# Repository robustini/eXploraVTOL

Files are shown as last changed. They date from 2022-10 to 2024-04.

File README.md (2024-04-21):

# eXplora Tailsitter VTOL

**Every single printable part of the project can be viewed in 3D on [OnShape](https://cad.onshape.com/documents/4c689e5b54cac6902d5813ec/w/fb80a5d05358b4e7959139db/e/8ae4df59a9bf6fdd0ec86a21)**

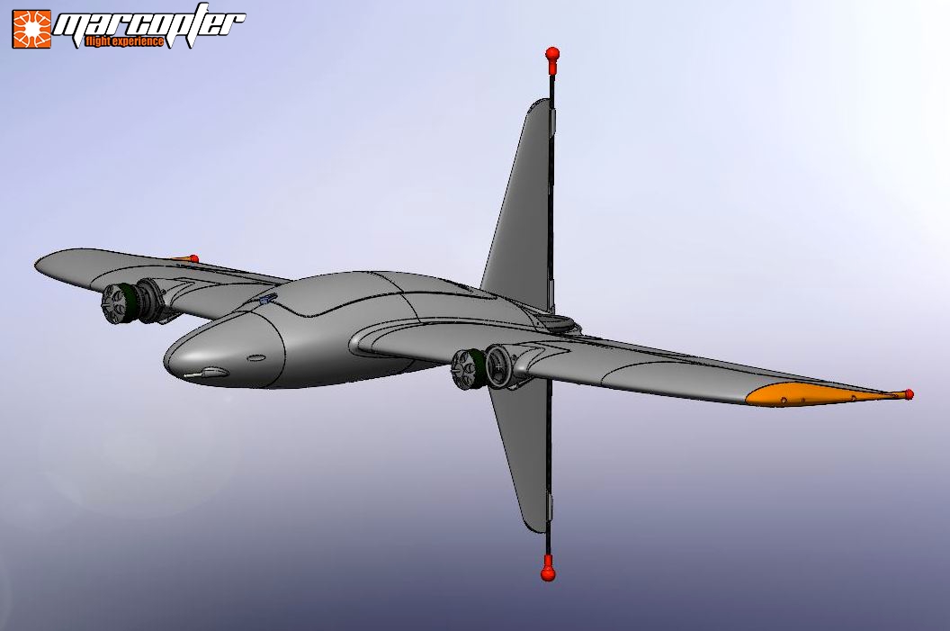
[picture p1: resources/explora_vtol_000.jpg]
eXplora Tailsitter VTOL


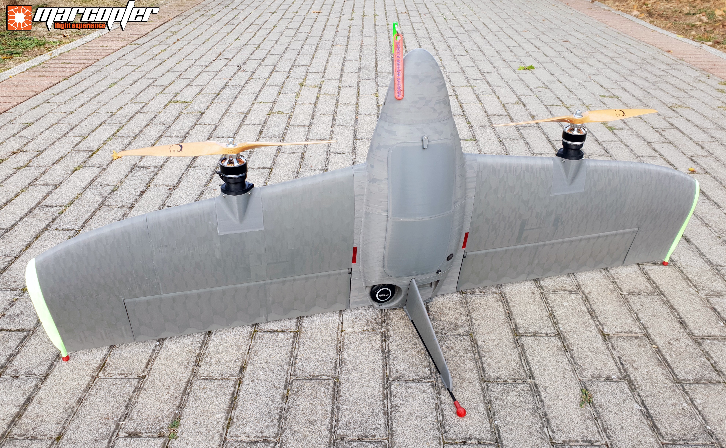
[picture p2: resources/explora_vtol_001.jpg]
eXplora Tailsitter VTOL


## Work in progress! ##

Given the massive requests we decided to make the repository public but it is still currently lacking documentation and specifications.

This will still give you the opportunity to view the entire project and print out all the individual components in order to finalize it.

We will complete the repository with everything we need as soon as possible.

To print the right wing you will need to mirror all the parts of the left wing in slicing, it is a very simple operation.

---

**eXplora Tailsitter VTOL** it was born from a concept by [Marco Robustini](https://www.linkedin.com/in/marco-robustini-a48a49a8/) four years ago.

Is a fully 3D printed vertical take-off UAS, a multi-role drone suitable for FPV, photogrammetry and other purposes, printed in PLA, ABS and TPU filament.

It comes in three formats: STL, 3MF and STEP, that way anyone can collaborate to improve it.

The slicing of this taislitter is complex, which is why all 3MF-format designs run with the powerful open source slicing software [SuperSlicer](https://github.com/supermerill/SuperSlicer) are provided.

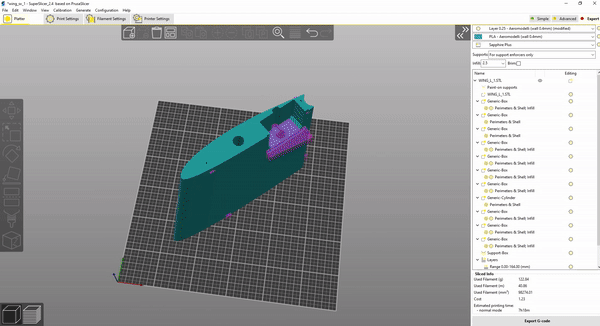
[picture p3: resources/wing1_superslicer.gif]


If you decide to use other slicing software such as [Cura](https://3dgbire.com/pages/ultimaker-cura) you should consider adding reinforcements at crucial points, taking a cue from the 3MF projects we provide as an example, compatible only with SuperSlicer and PrusaSlicer.
In this case you will not have to use this 3MFs but import the STLs into your slicing software.

We used the [Gyroid](https://3dsolved.com/3d-printing-with-gyroid-infills-all-you-need-to-know/) infill for most of the profiles, it comes from Nature, butterflies have an identical structure inside their wings, and Nature is never wrong.
It guarantees lightness and incredible strength.

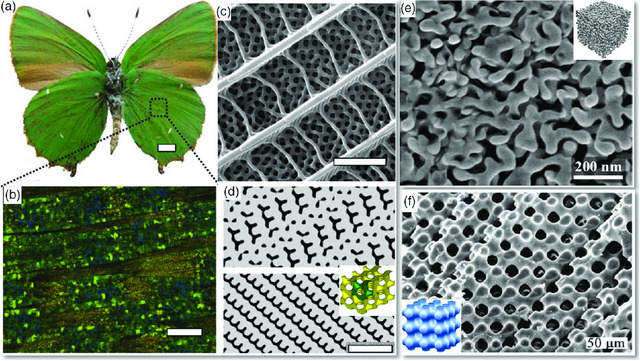
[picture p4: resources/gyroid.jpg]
Gyroid


## How it works and what it takes to finish it ##

eXplora Tailsitter VTOL it requires flight control and other electronic components to operate.

It has been tested with [Ardupilot](https://ardupilot.org) and [PX4](https://px4.io).

This is the provisional [BOM](https://github.com/robustini/eXploraVTOL/tree/main/resources/BOM.md) to complete the UAS, continuously being updated, absent for now of screws and nuts.

## Videos ##

- [The first version of eXplora](https://youtu.be/43UC-_kWp0w)
- [The second version of eXplora](https://youtu.be/K6R6v6_kQL0)
- [Flight tests of the V0.9.0](https://youtu.be/hy-UXrUSplU)
- [Full automatic mission](https://youtu.be/ne_7n9bvjYg)
- [Acro capability test](https://youtu.be/VbT0gd1w8IY)
- [Ardupilot: weathervaning feature](https://youtu.be/qcV7hz61uzA)
- [Ardupilot: QRTL](https://youtu.be/3Y-EviXewf0)

## User support ##

- [Discord channel](https://discord.gg/TCjNnfAEsB)
- [Ardupilot Discuss](https://discuss.ardupilot.org/t/explora-tailsitter-vtol-3d-printable-dual-motor-tailsitter/92341)

## How to get involved ##

- The eXplora Tailsitter VTOL project is open source and we encourage participation, if you can help in any way you are welcome!

- We have an active group of Beta Testers to help us improve our eXplora Tailsitter VTOL.

- Desired enhancements and issue can be posted to the [issues list](https://github.com/robustini/eXploraVTOL/issues).

- You can also open a [discussion](https://github.com/robustini/eXploraVTOL/discussions) to look for information or anything else.

## Simulation ##

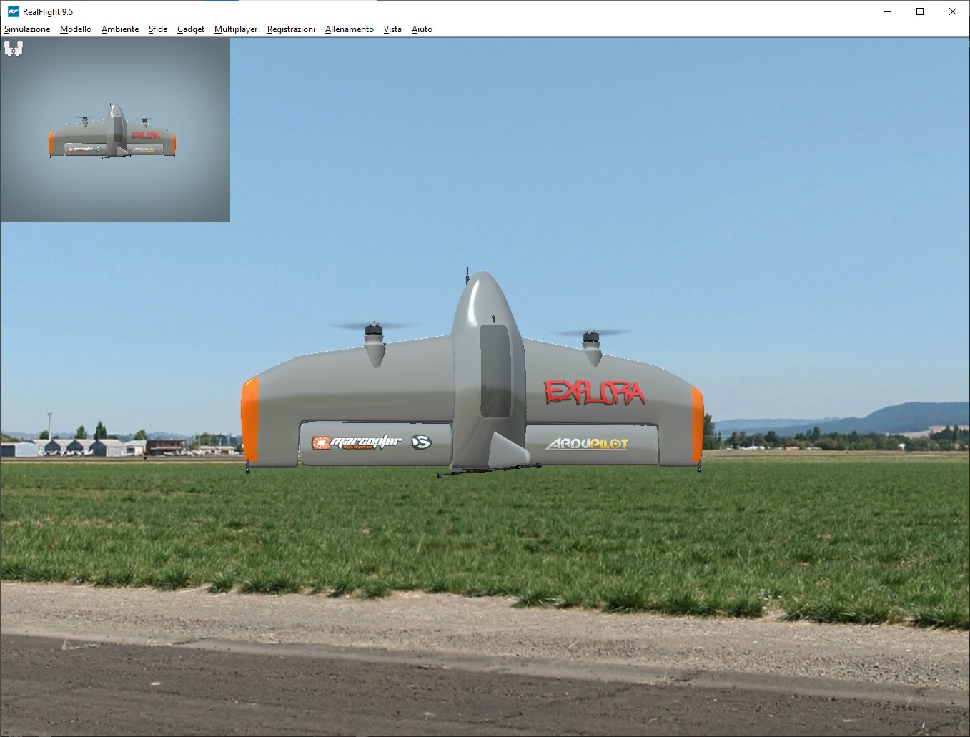
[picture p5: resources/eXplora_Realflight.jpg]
eXplora Tailsitter VTOL


If you would like to try our VTOL the [model](https://github.com/robustini/eXploraVTOL/tree/main/simulation/eXplora_Tailsiter_VTOL.RFX) for Realflight is available.

## The team ##

- [Davide Silimbani](https://www.linkedin.com/in/davide-silimbani/): 3d design
- [Roberto Casoni](https://www.linkedin.com/in/roberto-casoni-463a5914a/): test pilot
- [Lorenzo Franco](https://www.linkedin.com/in/lorenzing/): GCS support
- [Edoardo Nunzi](https://www.linkedin.com/in/edoardo-nunzi-8176a31a2/): FPV test pilot
- Antonios Antzoulatos: 3d print test
- [Brandon MacDougall](https://www.linkedin.com/in/brandon-macdougall-b273907/): Realflight model
- [Marco Robustini](https://www.linkedin.com/in/robustini/): concept design, SuperSlicer project, in-flight tuning and tests

## License ##

The eXplora Tailsitter VTOL project is licensed under the [GNU General Public License, version 3](https://github.com/robustini/eXploraVTOL/blob/main/LICENSE).

## Credits ##

We would like to publicly thank the development team of Ardupilot, and to all the beta testers who helped us.

## Donate ##

If you would like to support this project you can make a [donation](https://paypal.me/marcopter).

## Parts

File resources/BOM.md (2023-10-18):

# eXplora Tailsitter VTOL

## Bill of Materials ##

**Carbon tube:**

- 1 X Carbon tube: outer diameter 16mm, inner diameter 14mm, length 240mm
- 1 X Carbon tube: outer diameter 14mm, inner diameter 12mm, length 1000mm
- 2 X Carbon tube: outer diameter 10mm, inner diameter 8mm, length 469mm
- 2 X Carbon tube: outer diameter 5mm, inner diameter 3mm, length 43mm
- 1 X Carbon tube: outer diameter 5mm, inner diameter 3mm, length 600mm
- 2 X Carbon tube: outer diameter 4mm, inner diameter 2mm, length 56mm

**Propulsion:**

- 2 x GARTT ML 4112 480KV motor, or T-Motor Navigator MN4012 480kV, or equivalent (500W minimum)
- 2 x 14x8 beech wood propellers (length and pitch depend on the motor)
- 2 x 50A 6S ESC BlHeli32 with telemetry (alternatively 40A but not less)

**Servos:**

- 2 x SAVOX SC-1252MG Digital Servo (standard size) or equivalent/better

**Autopilot:**

- 1 x "Ardupilot" compatible flight control (Cube Orange, Pixhawk1 or equivalent), with its dedicated Power Module
- 1 x M8N GPS with compass, Here3 GPS GNSS, or better (alternatively double gps differently oriented)
- 1 x Airspeed Sensor MEAS Spec series (e.g. MS4525DO, MS5525), the analogs did not give good results
- 1 x BEC adequately sized on input/output voltage and maximum servo current, example input 25.2V (6S), output 6V, current 5A
- 1 x SiK Radio Telemetry or other type

**Optional:**

- 2 x JX8 connector, male and female
- 1 x TFmini Plus LIDAR

Various things, such as screws, nuts, power cables, servos extensions and others are not on the list at the moment, and still depend on the build type.

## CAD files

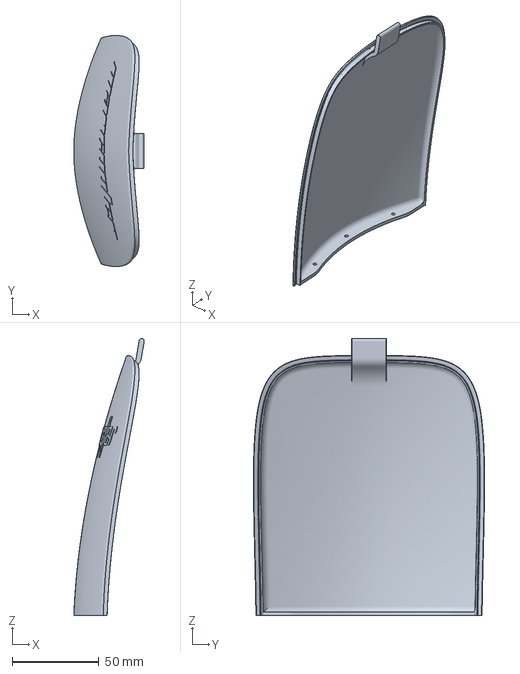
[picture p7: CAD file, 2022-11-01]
3MF/eXplora_VTOL_V1.00_Canopy_1.3mf
40.6 x 133.0 x 159.4 mm

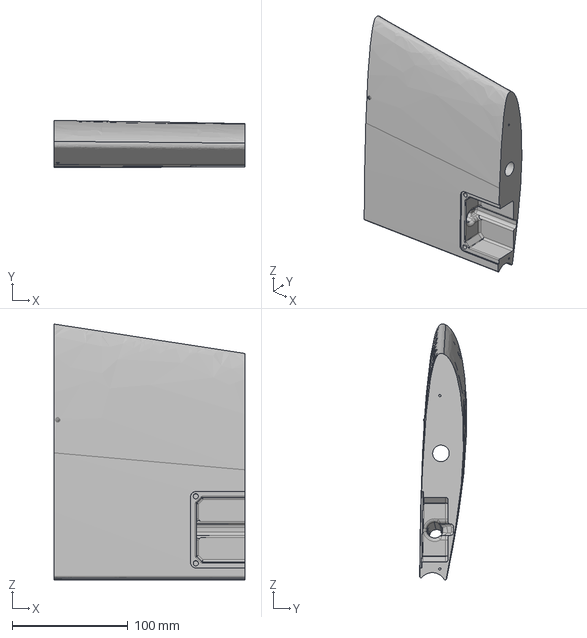
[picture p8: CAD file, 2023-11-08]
STEP/eXplora_VTOL_V1.00_Wing_L1.step
165.0 x 40.5 x 221.5 mm

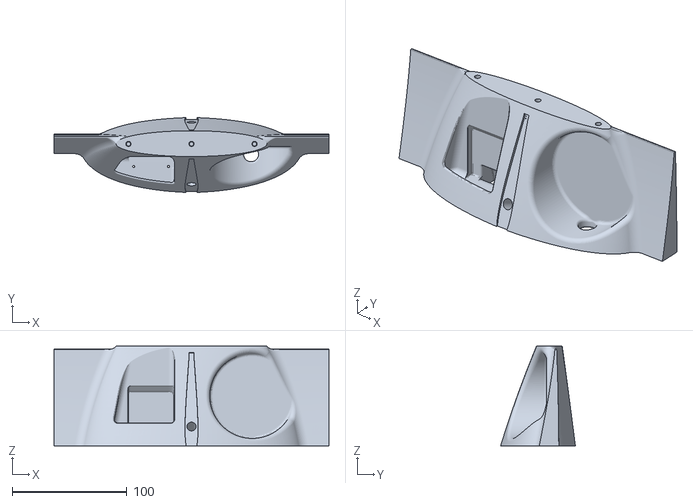
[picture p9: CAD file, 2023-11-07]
STL/eXplora_VTOL_V1.00_Fuselage_4_insert.stl
240.0 x 65.3 x 87.0

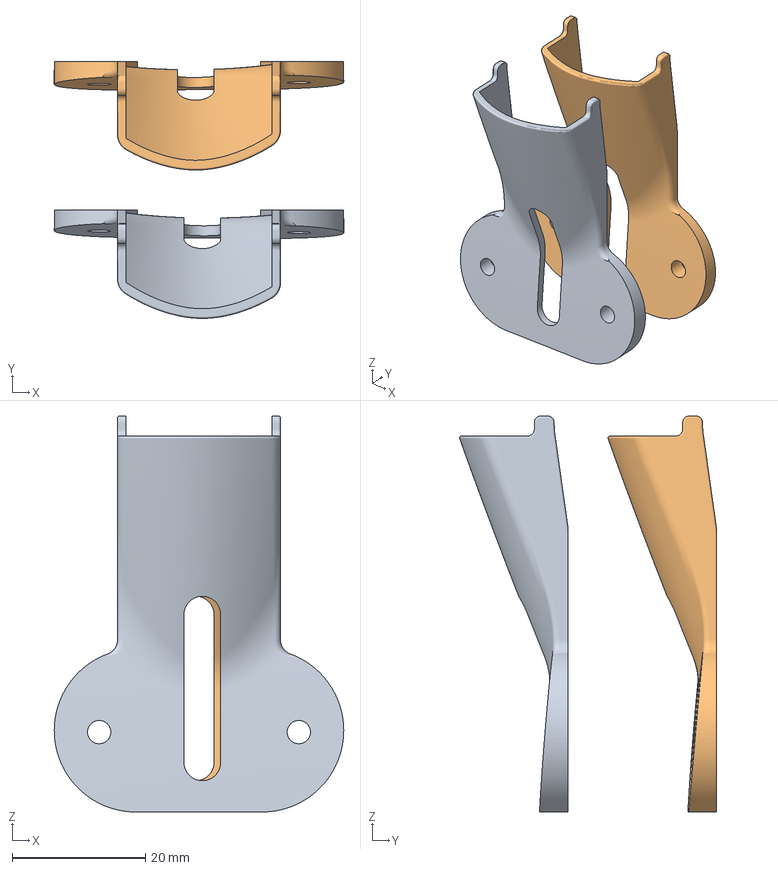
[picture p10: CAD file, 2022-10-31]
3MF/eXplora_VTOL_V1.00_ESC_cover_LR.3mf
43.5 x 38.6 x 59.5 mm
eXplora_VTOL_V1.00_ESC_cover_R.STL
eXplora_VTOL_V1.00_ESC_cover_L.STL

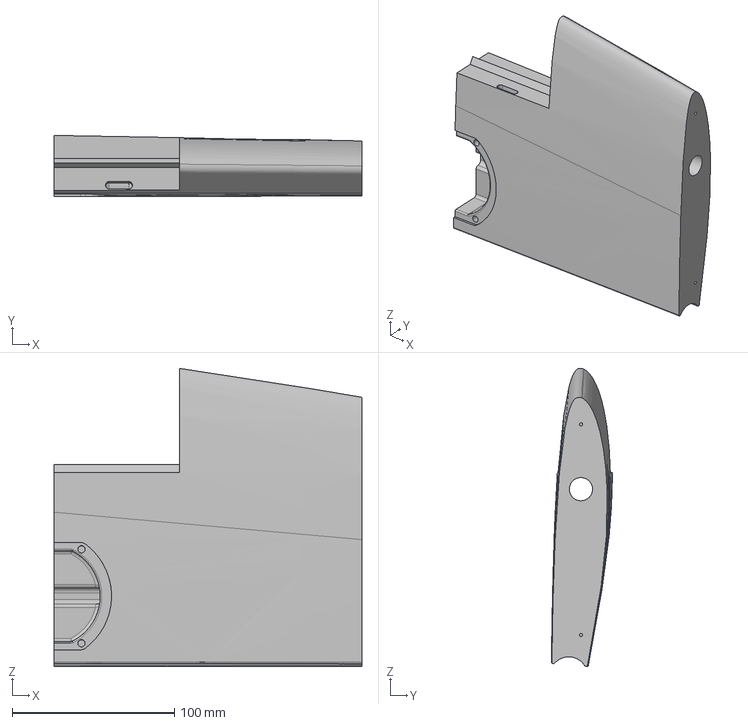
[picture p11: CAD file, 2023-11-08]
STEP/eXplora_VTOL_V1.00_Wing_L2.step
190.0 x 37.7 x 184.0 mm

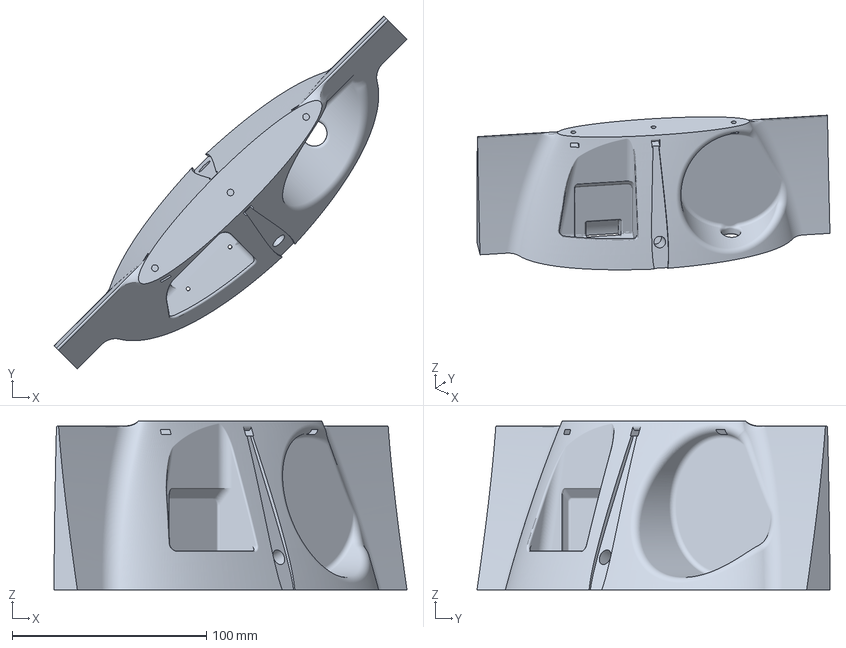
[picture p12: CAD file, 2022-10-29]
3MF/eXplora_VTOL_V1.00_Fuselage_4.3mf
181.7 x 181.7 x 87.0 mm

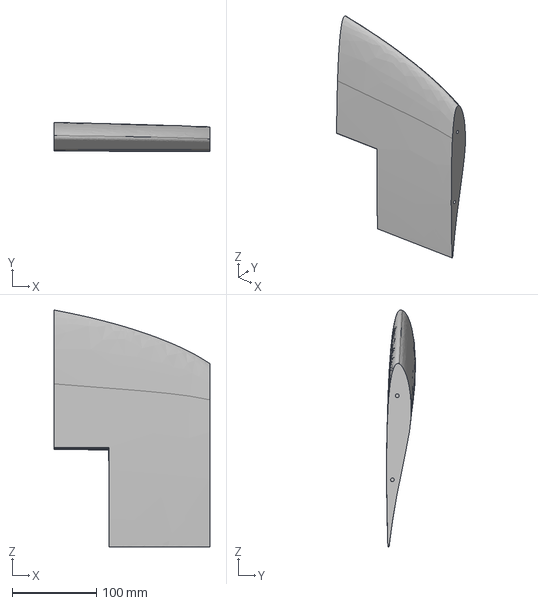
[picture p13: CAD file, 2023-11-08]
STEP/eXplora_VTOL_V1.00_Wing_L4.step
185.0 x 34.5 x 281.7 mm

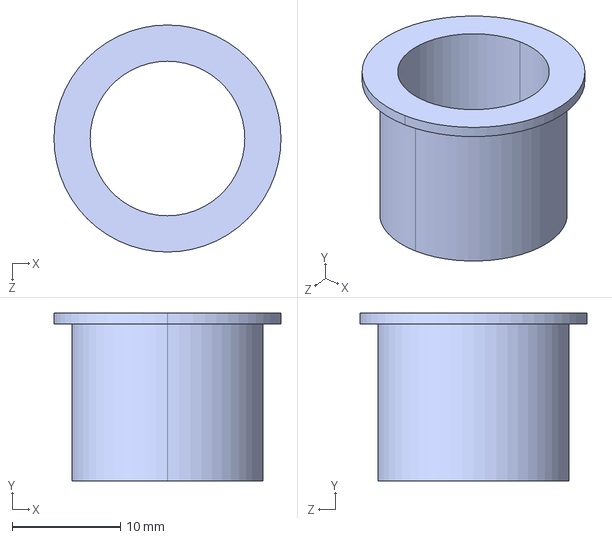
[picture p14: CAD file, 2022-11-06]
STEP/eXplora_VTOL_V1.00_14mm_Bayonet_Adapter_LR.step
21.0 x 15.5 x 21.0 mm

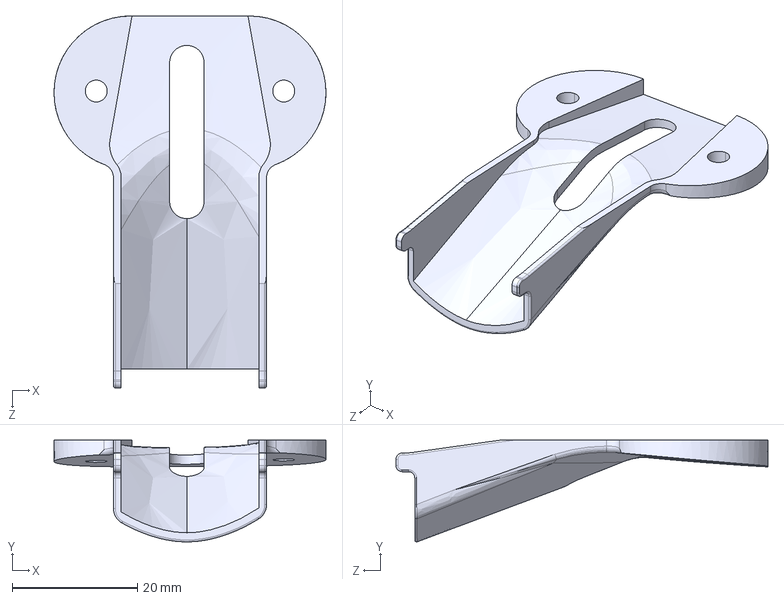
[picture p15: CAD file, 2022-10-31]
STEP/eXplora_VTOL_V1.00_ESC_cover_L.step
43.5 x 16.3 x 59.5 mm

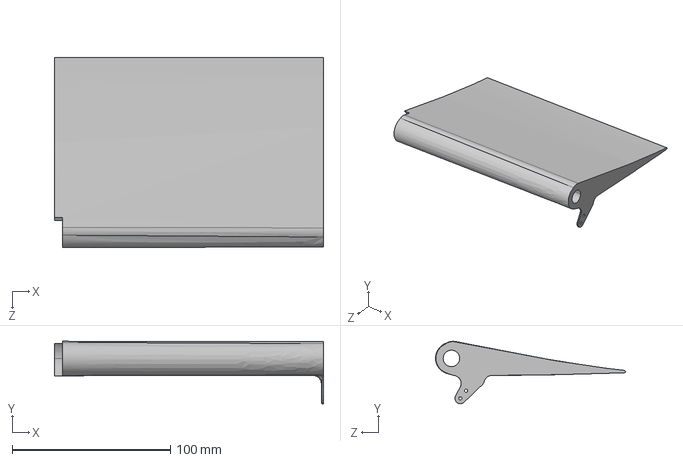
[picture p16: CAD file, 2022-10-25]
STEP/eXplora_VTOL_V1.00_Elevon_L1.step
170.0 x 39.5 x 120.1 mm

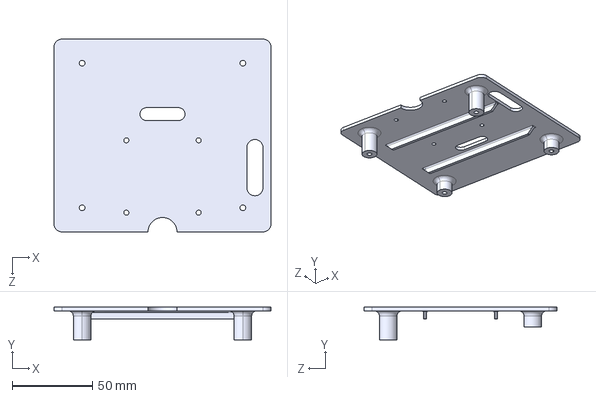
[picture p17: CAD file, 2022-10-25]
STEP/eXplora_VTOL_V1.00_FC_Housing.step
135.0 x 20.5 x 120.0 mm

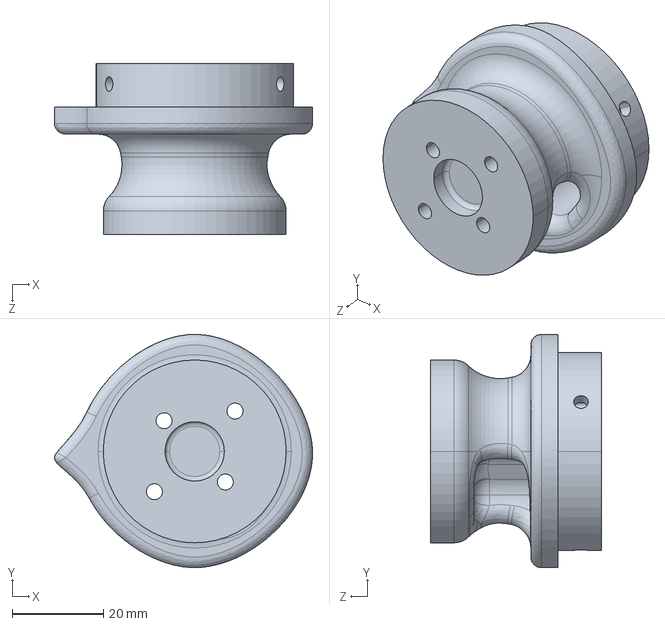
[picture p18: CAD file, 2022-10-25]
STEP/eXplora_VTOL_V1.00_Motor_Support_25x19_L.step
56.6 x 51.2 x 37.5 mm

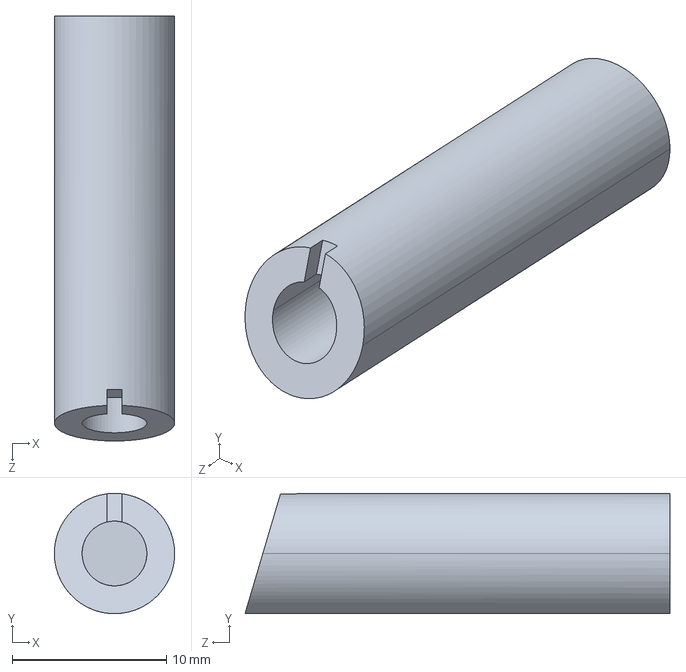
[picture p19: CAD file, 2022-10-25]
STEP/eXplora_VTOL_V1.00_Vertical_Stabilizer_4mm_Tube_Holder_Down.step
7.80 x 7.80 x 27.5 mm

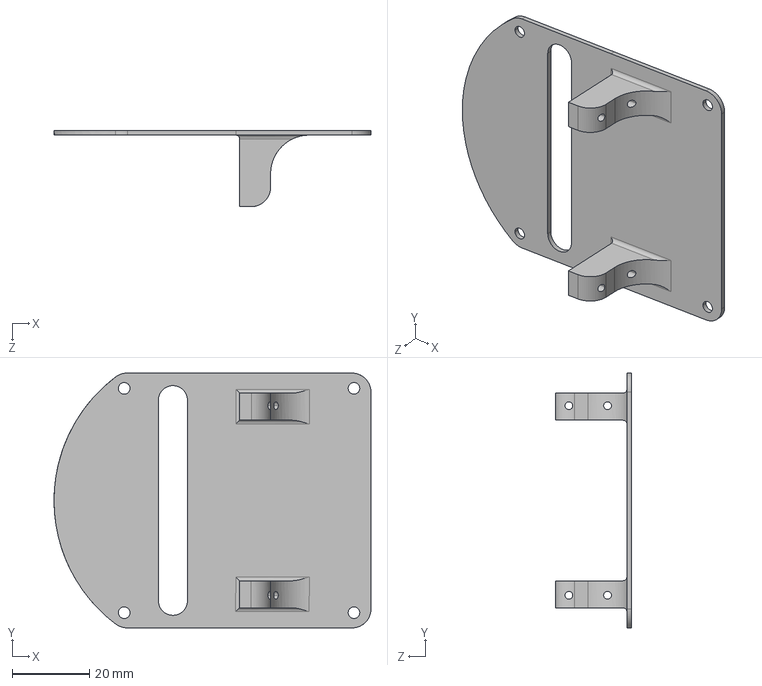
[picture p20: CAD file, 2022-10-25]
STEP/eXplora_VTOL_V1.00_Servo_Holder_LR.step
81.9 x 65.9 x 19.7 mm

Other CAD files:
STEP/eXplora_VTOL_V1.00_Wing_L3.step
STEP/eXplora_VTOL_V1.00_16mm_Bayonet_Adapter_LR.step
STEP/eXplora_VTOL_V1.00_Wing_L5.step
STEP/eXplora_VTOL_V1.00_Fuselage_Cable_Connector_Holder_L.step
3MF/eXplora_VTOL_V1.00_14mm_Bayonet_Adapter_LR.3mf
3MF/eXplora_VTOL_V1.00_16mm_Bayonet_Adapter_LR.3mf
3MF/eXplora_VTOL_V1.00_Canopy_2.3mf
3MF/eXplora_VTOL_V1.00_Canopy_Bracket.3mf
3MF/eXplora_VTOL_V1.00_Elevon_L1.3mf
3MF/eXplora_VTOL_V1.00_Elevon_L2.3mf
3MF/eXplora_VTOL_V1.00_Elevon_Lock_LR.3mf
3MF/eXplora_VTOL_V1.00_FC_Housing.3mf
3MF/eXplora_VTOL_V1.00_Fuselage_1.3mf
3MF/eXplora_VTOL_V1.00_Fuselage_5.3mf
3MF/eXplora_VTOL_V1.00_Fuselage_Cable_Connector_Holder_L.3mf
3MF/eXplora_VTOL_V1.00_Fuselage_Payload_Holder.3mf
3MF/eXplora_VTOL_V1.00_Motor_Support_19x25_L.3mf
3MF/eXplora_VTOL_V1.00_Motor_Support_25x19_L.3mf
3MF/eXplora_VTOL_V1.00_Motor_Support_25x25_L.3mf
3MF/eXplora_VTOL_V1.00_Pitot_cover.3mf
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

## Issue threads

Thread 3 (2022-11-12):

Wing size, batteries and AUW

kikislater, 2022-11-12:
Hi,

Thanks for this great work !
Could you please display in your readme (or bom for batteries) common informations to have an idea of performances, like :
- wing span, (1320mm I guess ?)
- AUW with selected batteries
- Flight time in hover
- Flight time in flying wing mode
- batteries Voltage (6S ?), C rating, mAh and/or batteries used

Thanks

robustini, 2022-11-12:
We still need to update the data, you can get this information on the Discord channel by comparing with those who are assembling it.

kikislater, 2022-11-12:
@robustini thanks, unfortunately discord invitation has expired

robustini, 2022-11-13:
https://discord.gg/TCjNnfAEsB

kikislater, 2022-11-21:
thanks

Closed 2022-11-12.

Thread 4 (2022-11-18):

add tilt rotors to front motors

stevereed66, 2022-11-18:
Hello,
Looks really good.
Not an issue,  are you planning on adding tilt rotor, gives much better  control in vtol mode.

I have  sidwinder 2 printer and have 3 tilt rotor  models eg  hee wing t1 ranger.

I  can setup arduplane as required.

If this is not in the plan  any idea's on modifications to nacles.There are lots of tilt mechanisms on thinki verse.

Thanks for great looking project

Steve

robustini, 2023-10-08:
I do not rule out creating a configuration with tiltable motors as well, although with the published STEPs I was hoping that such a modification could be implemented by someone else.

Closed 2024-09-20.

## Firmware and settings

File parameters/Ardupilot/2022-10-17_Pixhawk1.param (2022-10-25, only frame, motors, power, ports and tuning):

BATT_AMP_OFFSET,0
BATT_AMP_PERVLT,107.1766
BATT_ARM_MAH,0
BATT_ARM_VOLT,0
BATT_CAPACITY,5000
BATT_CRT_MAH,0
BATT_CRT_VOLT,0
BATT_CURR_PIN,3
BATT_FS_CRT_ACT,0
BATT_FS_LOW_ACT,4
BATT_FS_VOLTSRC,0
BATT_LOW_MAH,0
BATT_LOW_TIMER,10
BATT_LOW_VOLT,18.6
BATT_MONITOR,4
BATT_OPTIONS,0
BATT_SERIAL_NUM,-1
BATT_VLT_OFFSET,0
BATT_VOLT_MULT,10.7779
BATT_VOLT_PIN,2
BATT_WATT_MAX,0
BATT2_MONITOR,0
BATT3_MONITOR,0
BATT4_MONITOR,0
BATT5_MONITOR,0
BATT6_MONITOR,0
BATT7_MONITOR,0
BATT8_MONITOR,0
BATT9_MONITOR,0
FLTMODE_CH,8
FLTMODE1,7
FLTMODE2,19
FLTMODE3,5
FLTMODE4,17
FLTMODE5,12
FLTMODE6,0
INS_GYRO_FILTER,20
INS_HNTCH_ENABLE,0
Q_A_ACCEL_P_MAX,30000
Q_A_ACCEL_R_MAX,25000
Q_A_ACCEL_Y_MAX,27000
Q_A_ANG_LIM_TC,1
Q_A_ANG_PIT_P,3
Q_A_ANG_RLL_P,4
Q_A_ANG_YAW_P,3.5
Q_A_ANGLE_BOOST,0
Q_A_INPUT_TC,0.2
Q_A_RAT_PIT_D,0.005
Q_A_RAT_PIT_FF,0.2
Q_A_RAT_PIT_FLTD,10
Q_A_RAT_PIT_FLTE,0
Q_A_RAT_PIT_FLTT,16
Q_A_RAT_PIT_I,0.2
Q_A_RAT_PIT_IMAX,0.5
Q_A_RAT_PIT_P,0.17
Q_A_RAT_PIT_SMAX,50
Q_A_RAT_RLL_D,0.02
Q_A_RAT_RLL_FF,0.18
Q_A_RAT_RLL_FLTD,10
Q_A_RAT_RLL_FLTE,0
Q_A_RAT_RLL_FLTT,16
Q_A_RAT_RLL_I,0.15
Q_A_RAT_RLL_IMAX,0.5
Q_A_RAT_RLL_P,0.2
Q_A_RAT_RLL_SMAX,50
Q_A_RAT_YAW_D,0.01
Q_A_RAT_YAW_FF,0.2
Q_A_RAT_YAW_FLTD,0
Q_A_RAT_YAW_FLTE,2.5
Q_A_RAT_YAW_FLTT,16
Q_A_RAT_YAW_I,0.5
Q_A_RAT_YAW_IMAX,0.5
Q_A_RAT_YAW_P,0.4
Q_A_RAT_YAW_SMAX,50
Q_A_RATE_FF_ENAB,1
Q_A_RATE_P_MAX,75
Q_A_RATE_R_MAX,75
Q_A_RATE_Y_MAX,75
Q_A_SLEW_YAW,6000
Q_A_THR_MIX_MAN,0.9
Q_A_THR_MIX_MAX,0.9
Q_A_THR_MIX_MIN,0.1
Q_M_BAT_CURR_MAX,0
Q_M_BAT_CURR_TC,5
Q_M_BAT_IDX,0
Q_M_BAT_VOLT_MAX,0
Q_M_BAT_VOLT_MIN,0
Q_M_BOOST_SCALE,0
Q_M_HOVER_LEARN,2
Q_M_PWM_MAX,2000
Q_M_PWM_MIN,1000
Q_M_PWM_TYPE,4
Q_M_SAFE_DISARM,0
Q_M_SAFE_TIME,1
Q_M_SLEW_DN_TIME,0
Q_M_SLEW_UP_TIME,0
Q_M_SPIN_ARM,0
Q_M_SPIN_MAX,0.95
Q_M_SPIN_MIN,0.15
Q_M_SPOOL_TIME,0.25
Q_M_THST_EXPO,0.65
Q_M_THST_HOVER,0.2352654
Q_M_YAW_HEADROOM,200
SERIAL0_BAUD,115
SERIAL0_PROTOCOL,2
SERIAL1_BAUD,115
SERIAL1_OPTIONS,0
SERIAL1_PROTOCOL,2
SERIAL2_BAUD,115
SERIAL2_OPTIONS,0
SERIAL2_PROTOCOL,9
SERIAL3_BAUD,38
SERIAL3_OPTIONS,0
SERIAL3_PROTOCOL,5
SERIAL4_BAUD,115
SERIAL4_OPTIONS,0
SERIAL4_PROTOCOL,23
SERIAL5_BAUD,115
SERIAL5_OPTIONS,0
SERIAL5_PROTOCOL,16
SERVO1_FUNCTION,0
SERVO1_MAX,2000
SERVO1_MIN,1000
SERVO1_REVERSED,0
SERVO1_TRIM,1000
SERVO2_FUNCTION,0
SERVO2_MAX,2000
SERVO2_MIN,1000
SERVO2_REVERSED,0
SERVO2_TRIM,1000
SERVO3_FUNCTION,76
SERVO3_MAX,2000
SERVO3_MIN,1000
SERVO3_REVERSED,0
SERVO3_TRIM,1500
SERVO4_FUNCTION,75
SERVO4_MAX,2000
SERVO4_MIN,1000
SERVO4_REVERSED,0
SERVO4_TRIM,1500
SERVO5_FUNCTION,77
SERVO5_MAX,2000
SERVO5_MIN,1000
SERVO5_REVERSED,0
SERVO5_TRIM,1552
SERVO6_FUNCTION,78
SERVO6_MAX,2000
SERVO6_MIN,1000
SERVO6_REVERSED,1
SERVO6_TRIM,1495
SERVO7_FUNCTION,0
SERVO7_MAX,1900
SERVO7_MIN,1100
SERVO7_REVERSED,0
SERVO7_TRIM,1500
SERVO8_FUNCTION,0
SERVO8_MAX,1900
SERVO8_MIN,1000
SERVO8_REVERSED,0
SERVO8_TRIM,1500
SERVO9_FUNCTION,73
SERVO9_MAX,2000
SERVO9_MIN,1000
SERVO9_REVERSED,0
SERVO9_TRIM,1000

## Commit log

2022-10-25 First commits
    [2022-10-17_Pixhawk1.param, eXplora_VTOL_V1.00_16mm_Bayonet_Adapter_LR.3mf, eXplora_VTOL_V1.00_16mm_Bayonet_Adapter_LR.step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]
2022-10-25 Removed unnecessary part inside the STLs
    [eXplora_VTOL_V1.00_Wing_L5.stl, eXplora_VTOL_V1.00_Wing_L5_Long.stl]
2022-10-27 Submitted first BOM and updated readme
2022-10-29 Fix infill type in some sample 3MFs due to a bug in SuperSlicer
    [eXplora_VTOL_V1.00_Elevon_L1.3mf, eXplora_VTOL_V1.00_Elevon_L2.3mf, eXplora_VTOL_V1.00_Fuselage_1.3mf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]
2022-10-31 Added ESC cover
    [eXplora_VTOL_V1.00_ESC_cover_L.stl, eXplora_VTOL_V1.00_ESC_cover_LR.3mf]
2022-10-31 Added ESC cover step
    [eXplora_VTOL_V1.00_ESC_cover_L.step]
2022-11-01 Correct slicing in the base
    Inserted two perimeters for the first 3mm as in elevon 2.
    [eXplora_VTOL_V1.00_Elevon_L1.3mf]
2022-11-01 Fixed brim
    [eXplora_VTOL_V1.00_Canopy_1.3mf, eXplora_VTOL_V1.00_Canopy_2.3mf]
2022-11-06 Added 14mm bayonet adapter
    [eXplora_VTOL_V1.00_14mm_Bayonet_Adapter_LR.3mf, eXplora_VTOL_V1.00_14mm_Bayonet_Adapter_LR.step, eXplora_VTOL_V1.00_14mm_Bayonet_Adapter_LR.stl]
2023-10-18 Update BOM.md
    Corrected the servos specs, the previous ones were "mini", not standard
2023-11-07 Fuselage 4 with brass inserts
    Fuselage 4 alternative, instead of nuts insert M3 brass insert seats.
    [eXplora_VTOL_V1.00_Fuselage_4_insert.stl]
2023-11-08 Updated steps with M3 brass inserts
    eXplora_VTOL_V1.00_Fuselage_2.step
    eXplora_VTOL_V1.00_Fuselage_3.step
    eXplora_VTOL_V1.00_Wing_L1.step
    eXplora_VTOL_V1.00_Wing_L2.step
    eXplora_VTOL_V1.00_Wing_L4.step
    [eXplora_VTOL_V1.00_Wing_L1.step, eXplora_VTOL_V1.00_Wing_L2.step, eXplora_VTOL_V1.00_Wing_L4.step]
2023-11-08 Updated STL with M3 brass inserts
    [eXplora_VTOL_V1.00_Wing_L2.stl, eXplora_VTOL_V1.00_Wing_L4.stl]
